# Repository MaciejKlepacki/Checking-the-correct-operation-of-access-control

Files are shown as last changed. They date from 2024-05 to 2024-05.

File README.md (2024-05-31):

# Validation of Access Control Readers

## Project Objective and General Operation
The goal of this project was to automate the validation process of card readers and keypads within an access control system. When producing readers on a large scale, a small percentage of devices may not function correctly.

The entire setup is divided into two segments:
1. **Keypad Validation Segment:** This segment tests the proper functioning of the reader's keypad by pressing the appropriate keys. 

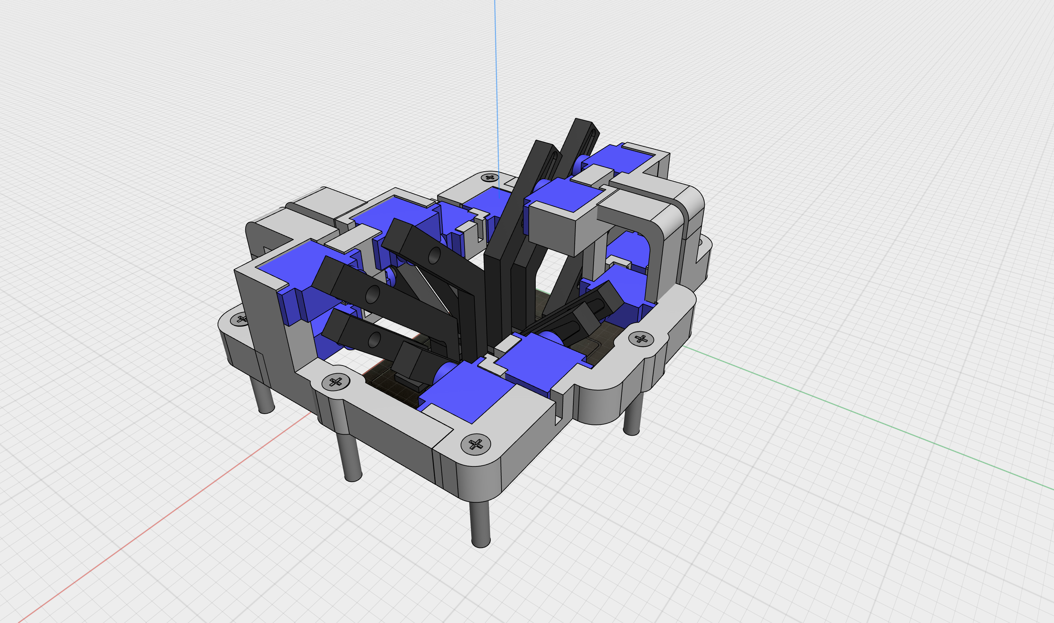
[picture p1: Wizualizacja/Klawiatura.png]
klawiatura
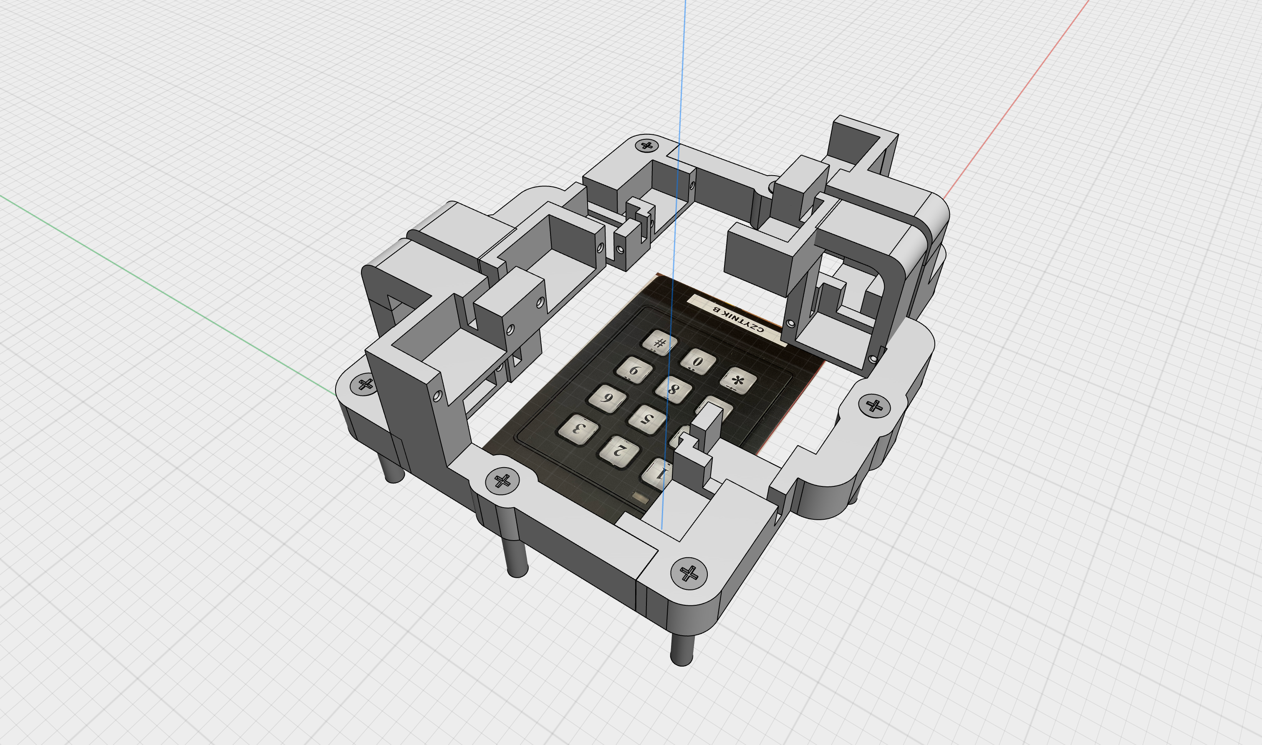
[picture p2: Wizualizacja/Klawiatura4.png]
klawiatura4
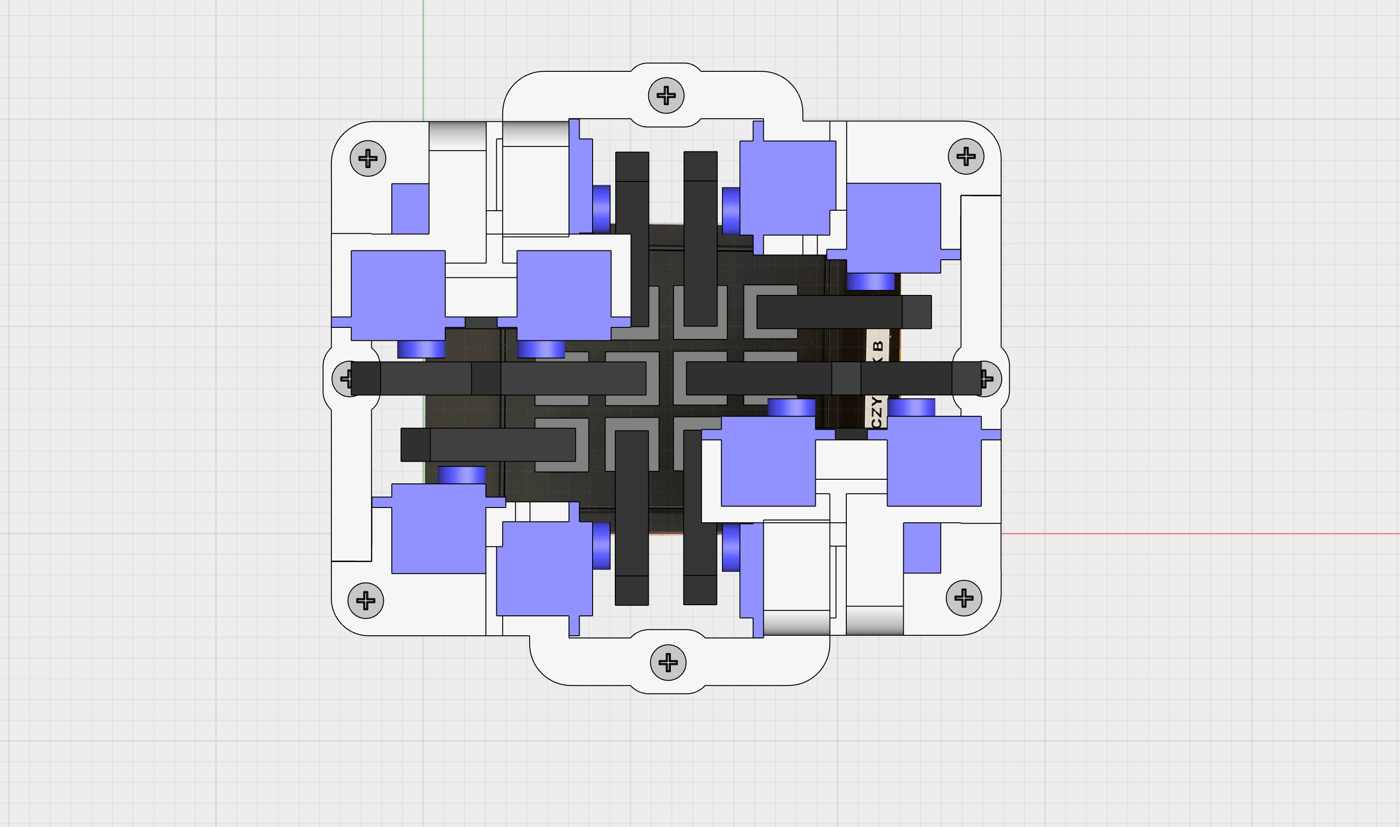
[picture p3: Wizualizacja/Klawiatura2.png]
klawiatura2
     

2. **Card Reader Validation Segment:** This segment tests the proper functioning of four access control card readers by presenting various cards to them.

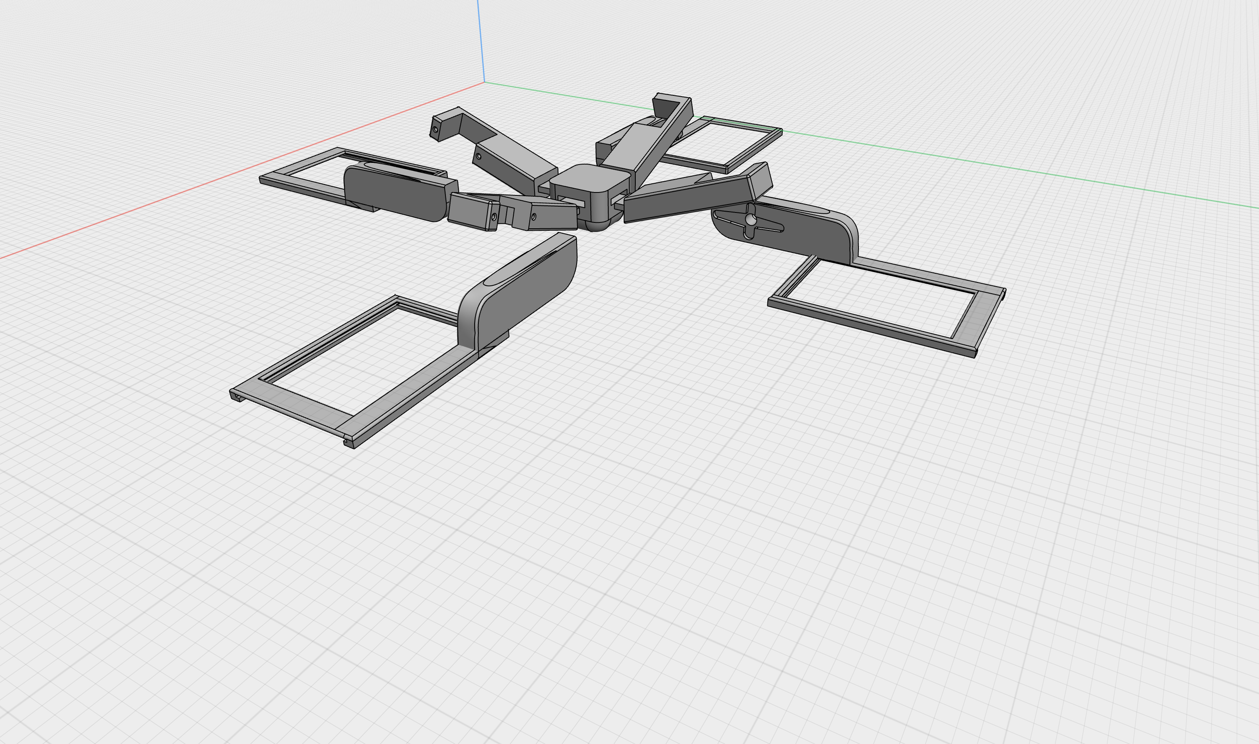
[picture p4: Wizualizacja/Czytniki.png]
czytniki
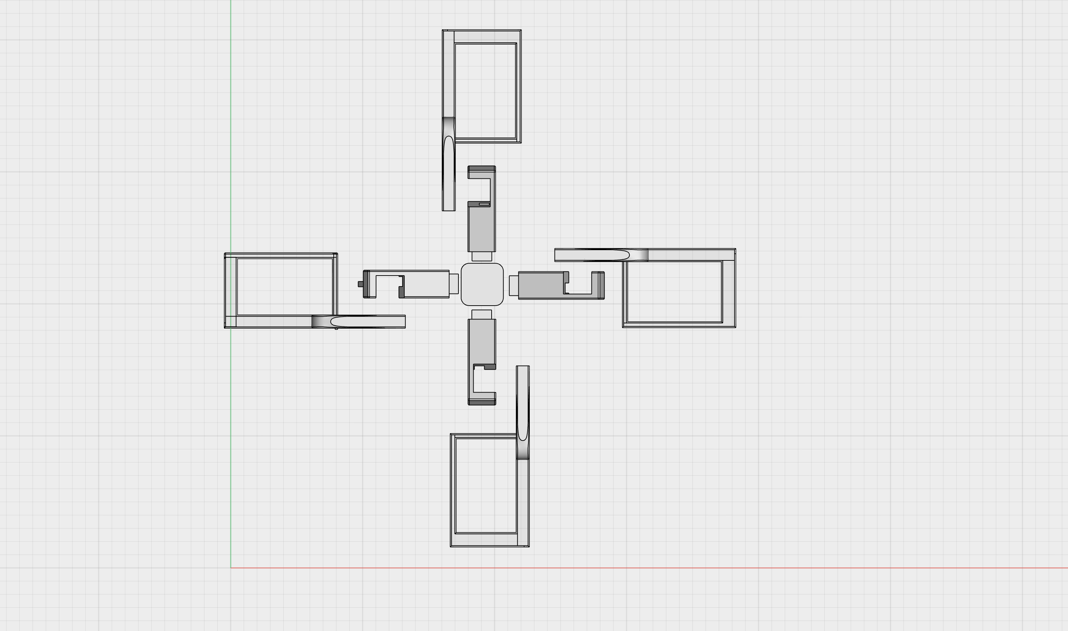
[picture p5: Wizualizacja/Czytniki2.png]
czytniki2
  

The core of the electronic system is an Arduino UNO with an Ethernet Shield. Control is carried out through a web browser by entering the appropriate IP address within the same network. By entering the address or pressing the appropriate button in the browser, the Arduino sets the proper output states, causing the specified task to be executed.

## Hardware
**Components Used:**
- Arduino UNO
- Ethernet Shield 2
- SD Card
- 12V Power Supply
- 2x NO (Normally Open) Buttons
- 19x SG-90 Servos
- 12V-5V Transformer
- 5V to 15V Step-up Transformer in DIP Package
- Stepper Motor
- PCA9685 PWM Driver Module
- Wires
- PCB Board

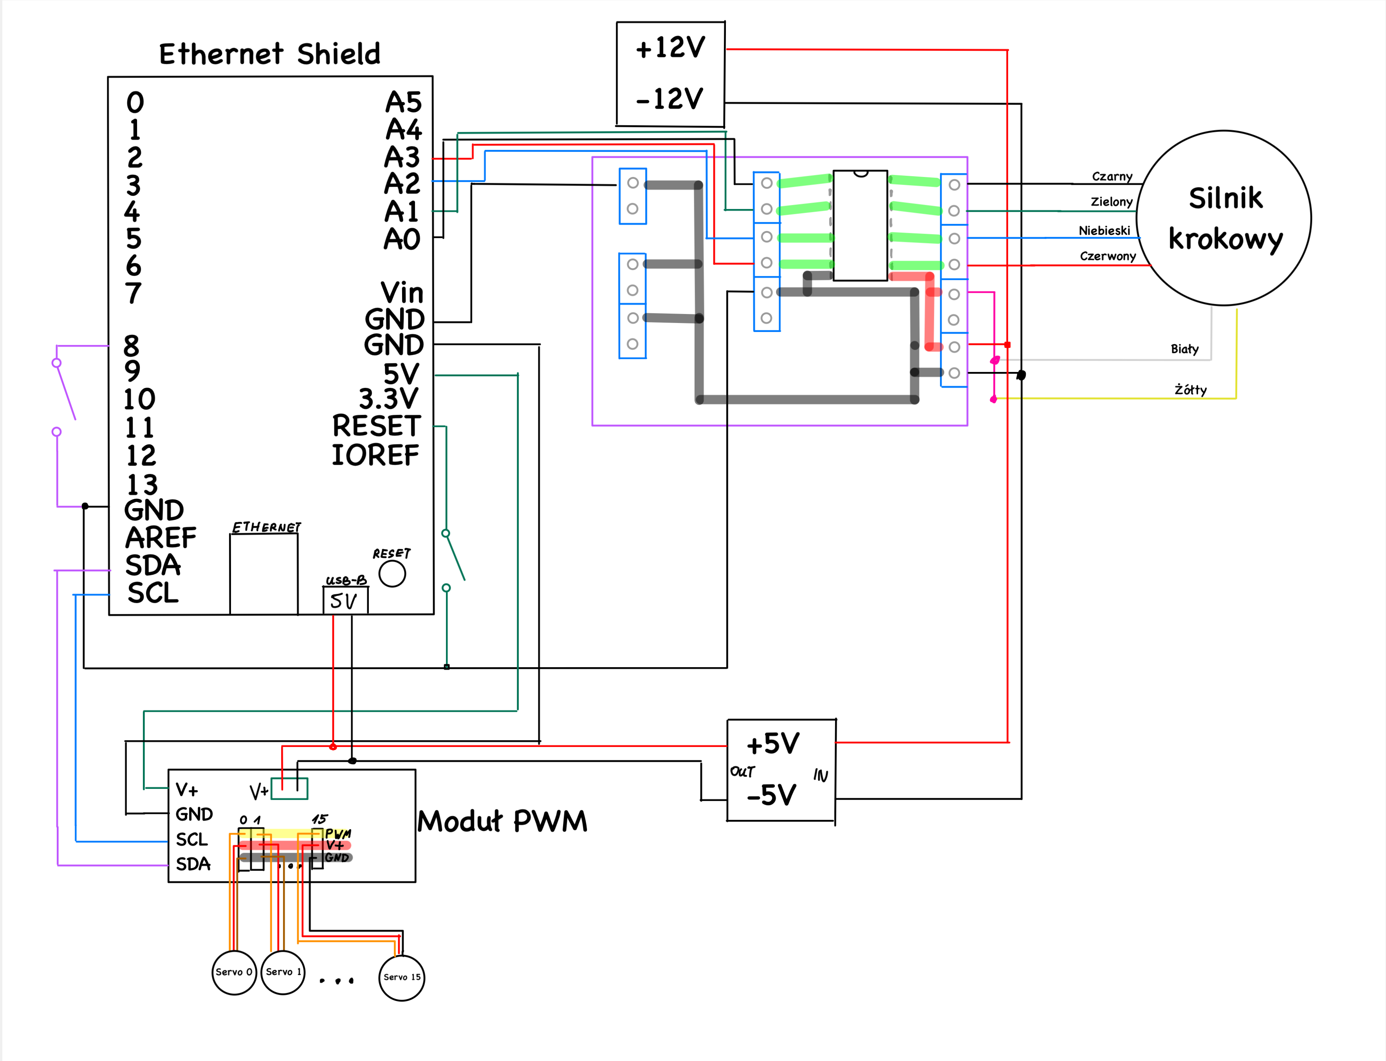
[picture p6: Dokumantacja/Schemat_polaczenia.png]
obwod


## Software
The main program is written in the Arduino language, which is based on C. The program is named [Sprawdzanie_czytnikow.ino](program_niskopoziomowy/Sprawdzanie_czytnikow.ino) and includes functions such as zeroing the position of motors, implementing various libraries, network settings, defining inputs/outputs, and initiating communication with the module via the I2C bus. The [HTML, CSS, and JS](Witryna) code for the web page should be uploaded to the SD card and inserted into the Arduino.

## Example

  **Entering the Appropriate IP Address in the Browser:**
   By default, this is set to `10.0.0.20`, but it can be changed in the [Sprawdzanie_czytnikow.ino](program_niskopoziomowy/Sprawdzanie_czytnikow.ino) code. The following page appears:   
   
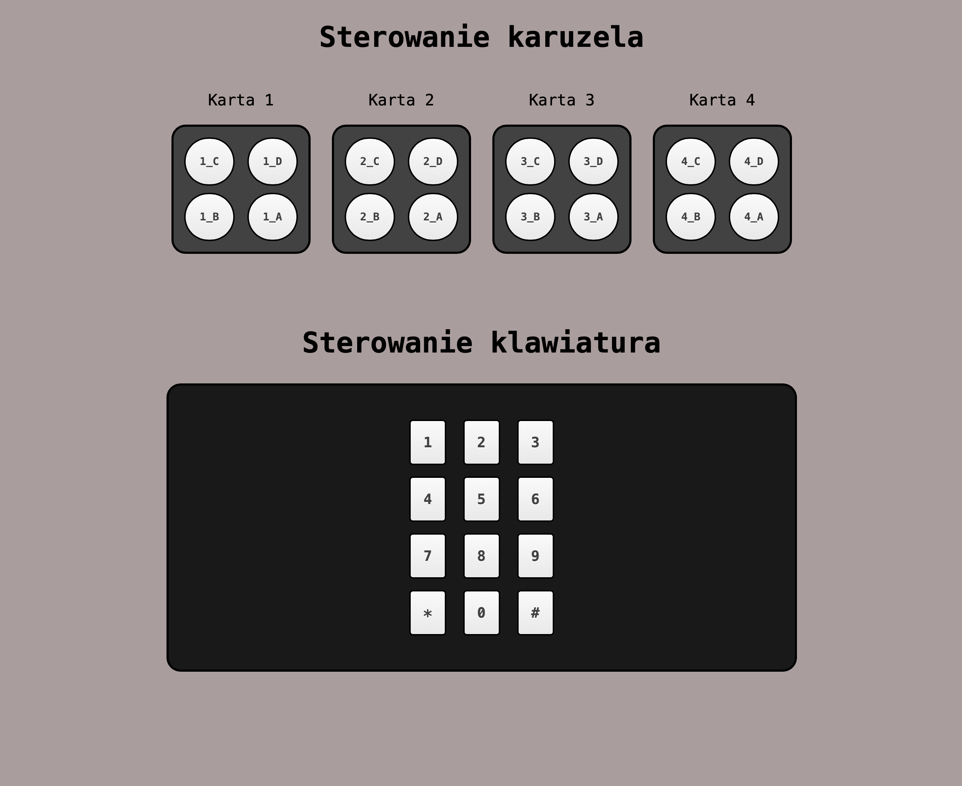
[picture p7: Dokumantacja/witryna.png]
witryna
   

2. **Testing a Reader Labeled 'B' by Presenting Card Number 4:**
   Select `4_B`. The mechanism rotates so that card 4 is positioned over reader B. The card is then moved closer to and away from the reader.

3. **Entering Code `1234#` on the Keypad:**
   Select `1`. The Arduino sends information to the PWM driver, which signals the first servo to move to the appropriate position, then return to default. The remaining combination is selected in a similar manner.

## Final results

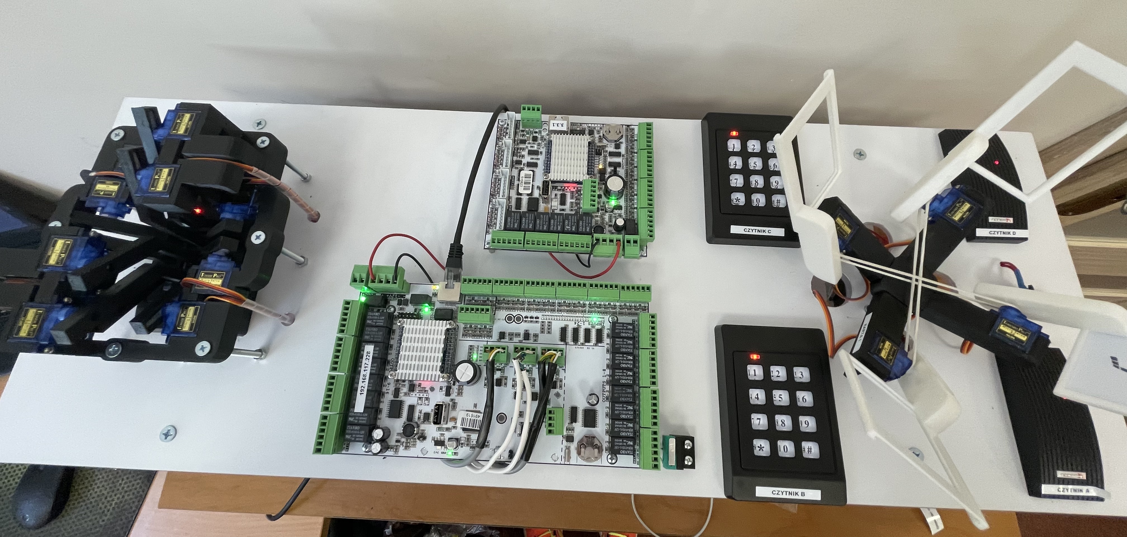
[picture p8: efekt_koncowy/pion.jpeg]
pion


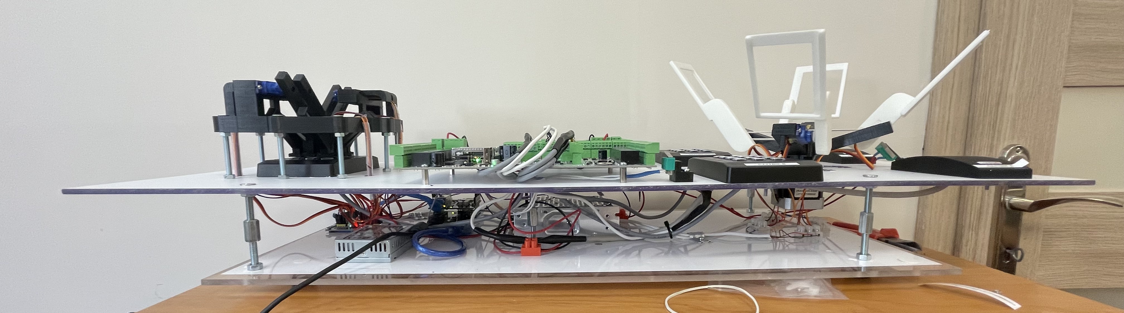
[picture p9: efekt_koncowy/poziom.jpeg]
poziom


### In the future, a high-level program will automatically send commands to the Arduino and verify whether the card was read correctly.

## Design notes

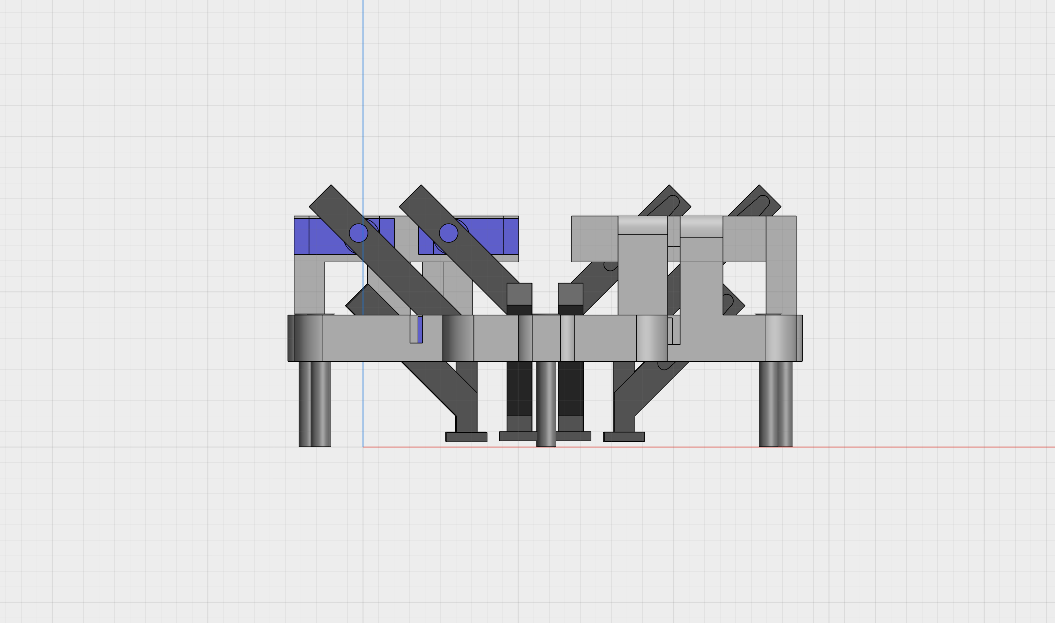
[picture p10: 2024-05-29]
Wizualizacja/Klawiatura3.png

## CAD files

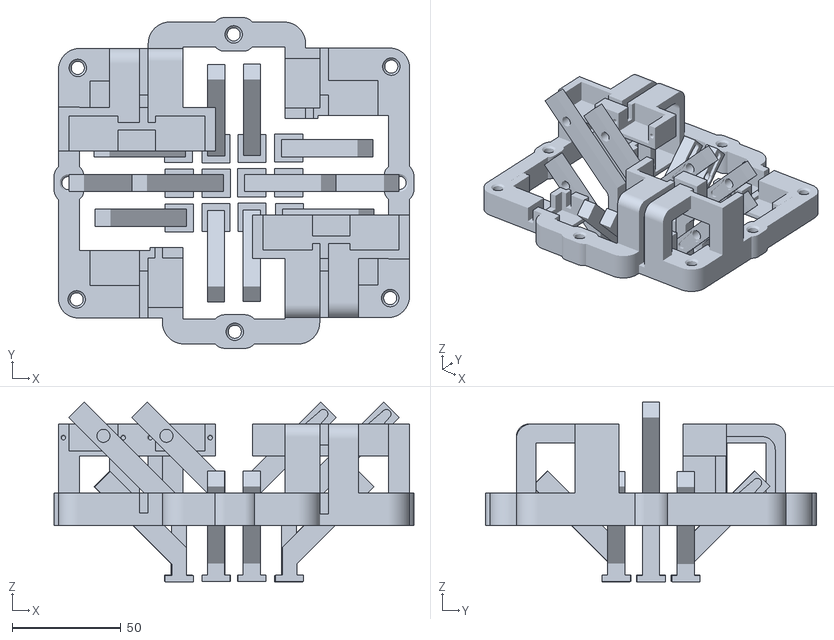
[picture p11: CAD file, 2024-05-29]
Druk 3D/Klawiatura bryła + ramiona.stl
165.6 x 152.2 x 82.8

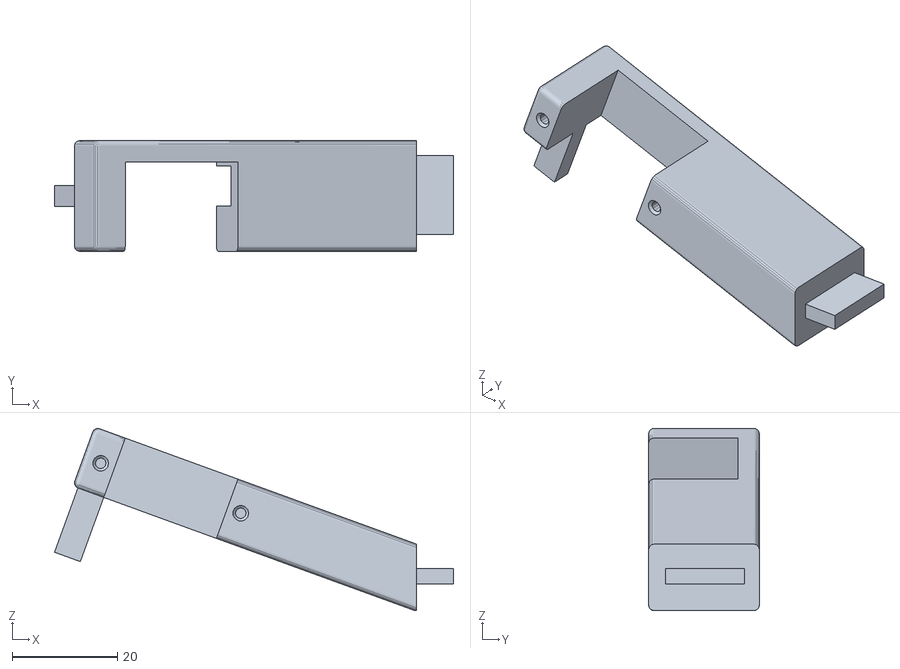
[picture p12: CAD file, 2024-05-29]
Druk 3D/ramię konfiguracyjne.stl
75.9 x 21.1 x 34.7

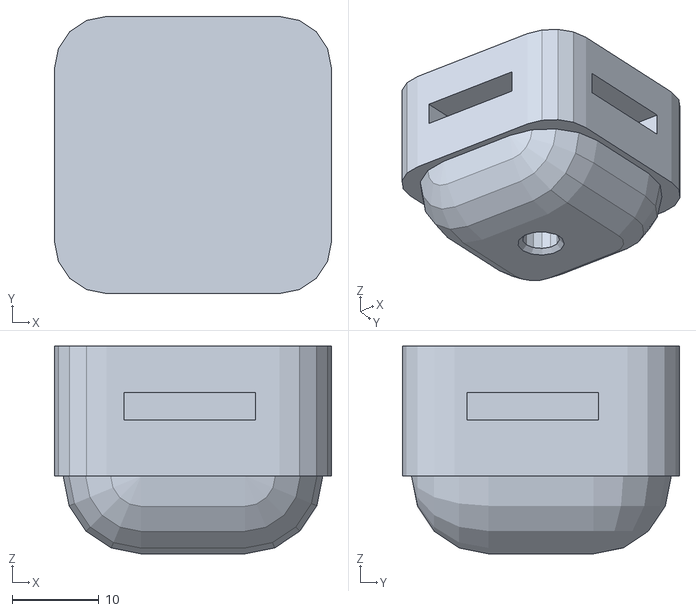
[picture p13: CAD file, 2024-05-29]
Druk 3D/środek.stl
32.0 x 32.0 x 24.0

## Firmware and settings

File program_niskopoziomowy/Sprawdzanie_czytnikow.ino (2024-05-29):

// dodawanie bibliotek
#include <SPI.h>
#include <Ethernet.h>
#include <Stepper.h>
#include <Wire.h>
#include <Adafruit_PWMServoDriver.h>

// ustawiena mudułu PWM
Adafruit_PWMServoDriver pwm = Adafruit_PWMServoDriver();


// ustawienia silnika
Stepper MojSilnik(200, A3, A2, A1, A0);
int destination = 0;
int position = 0;
int i = 0;


// ustawienia sieciowe
byte mac[] = { 0xDE, 0xAD, 0xBE, 0xEF, 0xFE, 0xED };
IPAddress ip(10, 0, 0, 20);  // Adres IP!!!
EthernetServer server(80);

void setup() {
  // definiowanie wyjść
  pinMode(8, INPUT_PULLUP);
  pinMode(A0, OUTPUT);
  pinMode(A1, OUTPUT);
  pinMode(A2, OUTPUT);
  pinMode(A3, OUTPUT);

  // nawiazywanie lacznosci arduino z komputerem, tworzenie serwera, nawiązywanie połączenia I2C z modułem PWM
  Serial.begin(9600);
  Ethernet.begin(mac, ip);
  server.begin();
  Serial.println("Server address:");
  Serial.println(Ethernet.localIP());
  pwm.begin();
  pwm.setOscillatorFrequency(27000000);
  pwm.setPWMFreq(50);  
  delay(10);

  // kalibrowanie serw
  pwm.setPWM(0, 0, 110); // klawiatura
  pwm.setPWM(1, 0, 175);
  pwm.setPWM(2, 0, 70);
  pwm.setPWM(3, 0, 75);
  pwm.setPWM(4, 0, 135);
  pwm.setPWM(5, 0, 80);
  pwm.setPWM(6, 0, 125);
  pwm.setPWM(7, 0, 145);
  pwm.setPWM(8, 0, 150);
  pwm.setPWM(9, 0, 77);
  pwm.setPWM(10, 0, 125);
  pwm.setPWM(11, 0, 135);
  pwm.setPWM(12, 0, 200); // karta
  pwm.setPWM(13, 0, 200);
  pwm.setPWM(14, 0, 200);
  pwm.setPWM(15, 0, 200);


  // kalibrowanie silnika głównego
  while (digitalRead(8) != LOW) {
    if (i < 200) {
      MojSilnik.setSpeed(20);
      MojSilnik.step(-1);
      i++;
    } else {
      digitalWrite(A0, LOW);
      digitalWrite(A1, LOW);
      digitalWrite(A2, LOW);
      digitalWrite(A3, LOW);
      exit(0);
    }
  }
  delay(500);
  MojSilnik.step(22);
  delay(500);
  digitalWrite(A0, LOW);
  digitalWrite(A1, LOW);
  digitalWrite(A2, LOW);
  digitalWrite(A3, LOW);
}


void loop() {
  while (digitalRead(8) != LOW) {
  // nawiązywanie połączenia
  EthernetClient client = server.available();
  if (client) {
    boolean currentLineIsBlank = true;
    String buffer = "";
     
    while (client.connected()) {
      if (client.available()) {
        char c = client.read();
        buffer += c;
        if (c == '\n' && currentLineIsBlank) {
          client.println("HTTP/1.1 200 OK");
          client.println("Content-Type: text/html");
          client.println("");
          break;
        }
        if (c == '\n') {
          currentLineIsBlank = true;
          buffer = "";

        }
        // rozpatrywanie warunkow
        else if (c == '\r') {
          // warunki karuzeli
          
          if (buffer.indexOf("GET /?status") >= 0) {
            if ((buffer.indexOf("GET /?status=1_A") >= 0) || (buffer.indexOf("GET /?status=2_B") >= 0) || (buffer.indexOf("GET /?status=3_C") >= 0) || (buffer.indexOf("GET /?status=4_D") >= 0)) {
              destination = 0;
            }
            if ((buffer.indexOf("GET /?status=1_B") >= 0) || (buffer.indexOf("GET /?status=2_C") >= 0) || (buffer.indexOf("GET /?status=3_D") >= 0) || (buffer.indexOf("GET /?status=4_A") >= 0)) {
              destination = 50;
            }
            if ((buffer.indexOf("GET /?status=1_C") >= 0) || (buffer.indexOf("GET /?status=2_D") >= 0) || (buffer.indexOf("GET /?status=3_A") >= 0) || (buffer.indexOf("GET /?status=4_B") >= 0)) {
              destination = 100;
            }
            if ((buffer.indexOf("GET /?status=1_D") >= 0) || (buffer.indexOf("GET /?status=2_A") >= 0) || (buffer.indexOf("GET /?status=3_B") >= 0) || (buffer.indexOf("GET /?status=4_C") >= 0)) {
              destination = 150;
            }
            MojSilnik.setSpeed(20);
            MojSilnik.step(destination - position);
            position = destination;
            if ((buffer.indexOf("GET /?status=1_A") >= 0) || (buffer.indexOf("GET /?status=1_B") >= 0) || (buffer.indexOf("GET /?status=1_C") >= 0) || (buffer.indexOf("GET /?status=1_D") >= 0)) {
              pwm.setPWM(12, 0, 320);
              delay(1500);
              pwm.setPWM(12, 0, 200);
            }
            if ((buffer.indexOf("GET /?status=2_A") >= 0) || (buffer.indexOf("GET /?status=2_B") >= 0) || (buffer.indexOf("GET /?status=2_C") >= 0) || (buffer.indexOf("GET /?status=2_D") >= 0)) {
              pwm.setPWM(13, 0, 320);
              delay(1500);
              pwm.setPWM(13, 0, 200);
            }
            if ((buffer.indexOf("GET /?status=3_A") >= 0) || (buffer.indexOf("GET /?status=3_B") >= 0) || (buffer.indexOf("GET /?status=3_C") >= 0) || (buffer.indexOf("GET /?status=3_D") >= 0)) {
              pwm.setPWM(14, 0, 320);
              delay(1500);
              pwm.setPWM(14, 0, 200);
            }
            if ((buffer.indexOf("GET /?status=4_A") >= 0) || (buffer.indexOf("GET /?status=4_B") >= 0) || (buffer.indexOf("GET /?status=4_C") >= 0) || (buffer.indexOf("GET /?status=4_D") >= 0)) {
              pwm.setPWM(15, 0, 320);
              delay(1500);
              pwm.setPWM(15, 0, 200);
            }
            digitalWrite(A0, LOW);
            digitalWrite(A1, LOW);
            digitalWrite(A2, LOW);
            digitalWrite(A3, LOW);

          // warunki klawiatury
          } else if (buffer.indexOf("GET /?kl") >= 0) {
            if (buffer.indexOf("GET /?kl=0") >= 0) {
              pwm.setPWM(0, 0, 95);
              delay(500);
              pwm.setPWM(0, 0, 110);
            }
            if (buffer.indexOf("GET /?kl=1") >= 0) {
              pwm.setPWM(1, 0, 190);
              delay(500);
              pwm.setPWM(1, 0, 175);
            }
            if (buffer.indexOf("GET /?kl=2") >= 0) {
              pwm.setPWM(2, 0, 85);
              delay(500);
              pwm.setPWM(2, 0, 70);
            }
            if (buffer.indexOf("GET /?kl=3") >= 0) {
              pwm.setPWM(3, 0, 90);
              delay(500);
              pwm.setPWM(3, 0, 75);
            }
            if (buffer.indexOf("GET /?kl=4") >= 0) {
              pwm.setPWM(4, 0, 150);
              delay(500);
              pwm.setPWM(4, 0, 135);
            }
            if (buffer.indexOf("GET /?kl=5") >= 0) {
              pwm.setPWM(5, 0, 90);
              delay(500);
              pwm.setPWM(5, 0, 80);
            }
            if (buffer.indexOf("GET /?kl=6") >= 0) {
              pwm.setPWM(6, 0, 110);
              delay(500);
              pwm.setPWM(6, 0, 125);
            }
            if (buffer.indexOf("GET /?kl=7") >= 0) {
              pwm.setPWM(7, 0, 130);
              delay(500);
              pwm.setPWM(7, 0, 145);
            }
            if (buffer.indexOf("GET /?kl=8") >= 0) {
              pwm.setPWM(8, 0, 130);
              delay(500);
              pwm.setPWM(8, 0, 150);
            }
            if (buffer.indexOf("GET /?kl=9") >= 0) {
              pwm.setPWM(9, 0, 63);
              delay(500);
              pwm.setPWM(9, 0, 77);
            }
            if (buffer.indexOf("GET /?kl=*") >= 0) {
              pwm.setPWM(10, 0, 92);
              delay(500);
              pwm.setPWM(10, 0, 125);
            }
            if (buffer.indexOf("GET /?kl=%") >= 0) {
              pwm.setPWM(11, 0, 105);
              delay(500);
              pwm.setPWM(11, 0, 135);
            }
            delay(10);
          }
        } else {
          currentLineIsBlank = false;
        }
      }
    }
    delay(1);
    client.stop();  // Zakończ serwer
  }
  }
  delay(500);
  MojSilnik.step(25);
  position = 0;
  destination = 0;
  digitalWrite(A0, LOW);
  digitalWrite(A1, LOW);
  digitalWrite(A2, LOW);
  digitalWrite(A3, LOW);
  delay(1000);
}
